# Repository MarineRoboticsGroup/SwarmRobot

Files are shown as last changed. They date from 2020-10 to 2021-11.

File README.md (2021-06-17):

# Swarm Robot

## Quick Start

This section will walk you through getting the software and networking set up for your robot to work. This assumes that your robot has been fabricated, assembled, and all components are properly connected. Much of the setup has been automated through the bash scripts provided in this repo. Start by cloning this repository into your home directory on the Intel Nuc and running the Nuc setup script.

### NUC Setup

<details>

This setup assumes that you have either Ubuntu 18.04 or 20.04 installed on the NUC. If not, I recommend following the official Ubuntu tutorials on [installing Ubuntu desktop from USB flash drive](https://ubuntu.com/tutorials/install-ubuntu-desktop#4-boot-from-usb-flash-drive) and [creating a bootable USB stick](https://ubuntu.com/tutorials/create-a-usb-stick-on-windows#1-overview).

Once this is done, the following instructions will walk you through the necessary steps to set up the NUC.

``` BASH
cd ~
git clone https://github.com/MarineRoboticsGroup/SwarmRobot.git swarm-robot
cd ~/swarm-robot/install
bash ./nucinstall.sh
```

**The bash script may sometimes fail while building the catkin workspace.** In this case: close the terminal, open a new terminal, and rerun `bash ./nucinstall.sh`

This will install all of the basic packages required, create a catkin workspace, clone all of the required repositories into this workspace, build the workspace, and remove the original repo cloned into the home directory. In addition, this performs some of the necessary network configurations of the Nuc to allow for use of this robot in a multi-robot network.

Then to allow for the robots to operate over a common network, change the namespace variables in the robot launch files such that each robot has a unique namespace. In general you can do this by changing the line `<arg name="namespace" default="mrg1" />` to `<arg name="namespace" default="<this robot's unique namespace name>" />`.

As of now the launch file(s) required to change are:

- ~/catkin_ws/src/swarm-robot/ros/launch/swarm_teleop.launch (Line 2)
- ~/catkin_ws/src/dynamixel-workbench/dynamixel_workbench_controllers/launch/dynamixel_controllers.launch (Line 4)
- ~/catkin_ws/src/orb_slam_2_ros/ros/launch/orb_slam2_d435_rgbd.launch (Lines 2, 8, 9)
- ~/catkin_ws/src/swarmbot_controller/launch/position_controller.launch (Line 2)

In addition, you will need to modify the ROS environment variables which specify the IP address of the ROS master and the NUC you are currently using. This was partially done in the install file, but the values will need to be modified to suit your desired setup and the specific IP of the NUC you are working on. This setup guide will cover the desired IP addresses you will want to set for several possible situations.

It will be valuable to know the `ifconfig` terminal command and understand which entries correspond to wireless and wired networks. Generally, if the network interface name starts with 'wl' (e.g. 'wlp0s20f3') then it is a wireless network. If the network interface name starts with 'en' (e.g. 'enp7s0f1') then it is an ethernet connection. Note that the format of the device name varies based on the operating system being used, so may not comply with the patterns shown above.

First open your `.bashrc` file in any editor and navigate to the bottom of the file.

``` BASH
nano ~/.bashrc
```

You will see two lines which look like this, where the values in <> are actually temporary values you will **need to change**:

``` BASH
echo "export ROS_IP=<Current NUC IP>" >> ~/.bashrc
echo "export ROS_MASTER_URI=http://<Master IP>:11311" >> ~/.bashrc
```

### IP Address options (NUC Setup)

<details>

#### Running a connected network with a separate computer

This is the most recommended and expected setup, where you will run the robots in a connected network. In this arrangement there will be an additional computer (either a laptop or a desktop which is connected to the same network shared by all of the NUCs) which will be the ROS master. In this scenario you will set the following:

\<Current NUC IP> = the IP address of the NUC on the shared wireless network.
\<Master IP> = the IP address of the connected laptop or desktop on the shared wireless network.

#### Running a connected network without a separate computer

This is like the previous scenario but without the additional computer, which one would likely use for monitoring. It is not immediately clear why someone would want to do this, but it will be listed anyways.

\<Current NUC IP> = the IP address of the NUC on the shared wireless network.
\<Master IP> = the IP address of any of the NUCs on the shared wireless network. **Note**: It is important that in this configuration that all robots must have the same \<Master IP> address.

#### Running a single robot

If you intend to only run this robot independently without having it connected to any other computers over a wireless network then you can set the `Current NUC IP` and `Master IP` to the same values. This could apply to a situation where you are running multiple robots but they are not connected with eachother and are running independently of one another. Such a scenario is possible in locations where it is difficult to establish a wireless network for one reason or another.

In this configuration we're assuming that the NUC is not connected to a wireless network at all.

\<Current NUC IP> = the IP address of the NUC on the shared ethernet network.
\<Master IP> = the IP address of the NUC on the shared ethernet network.

</details>

#### Configure the connection between NUC and Nano (NUC)

Next, you will want to configure the ethernet connection between the Intel NUC and the Jetson Nano. The easiest way to do this is by first making sure the Nano is powered on and connected to the NUC via ethernet. Then open your connections as such:

``` BASH
nm-connection-editor
```

Edit the wired connection between the NUC and the Nano (commonly named 'Wired Connection 1') and navigate to the IPv4 Settings Tab. Change method to `Shared to other computers` and click in the table of addresses to add a new entry. Set the entry to the following values - Address: 10.42.0.1 / Netmask: 24 / Gateway: (leave empty). This will set it such that the IP address of the NUC on the network made over this ethernet connection will always be `10.42.0.1`.

This can be done for all of the NUCs on the network, and will not cause any issues. This is because this is only their IP address for the local network connection they have with their connected Nano, so this IP address will not be reachable for any of the other NUCs in the larger ROS network. The connections between all of the NUCs on the ROS network will be shared over some local wireless network, on which it will have a separate IP address from the local ethernet network it shares with the Nano.

Finally, for convenience it is recommended to disable automatic updates, as described in [this line](https://www.omgubuntu.co.uk/2016/02/how-to-disable-automatic-update-ubuntu).

</details>

### Nano Setup

<details>

The nano setup should be mostly uninvolved. This setup assumes that the Jetson Nano has already been setup and is bootable. If not, follow [this tutorial](https://developer.nvidia.com/embedded/learn/get-started-jetson-nano-devkit#intro) to get started with the Nano.

We will first run a setup script that installs the necessary libraries for the Nano to work with the RealSense Camera.

``` BASH
cd ~
git clone https://github.com/MarineRoboticsGroup/SwarmRobot.git swarm-robot
cd ~/swarm-robot/install
bash ./nanoinstall.sh
```

*If having issues try running `bash ./nanoinstall.sh` again*. Sometimes it doesn't fully install the first time.

From here we just need to set up the wired connection between the Nano and the NUC. Make sure that there is an ethernet connecting the two devices and then open the connections configurations with the following command.

``` BASH
nm-connection-editor
```

There should be a single connection profile that says something like 'Wired Connection 1'. Edit this connection. Navigate to the `IPv4 Settings` tab. Change `Method` to *Manual*. In the Addresses table set the first (and only) row item to `Address = 10.42.0.25 | Netmask = 24 | Gateway = 10.42.0.1`.

This should be all that is necessary to set up on the Nano for our base configuration. You should check that the connection between the NUC and Nano is functioning by first trying to ping the NUC from the nano: `ping 10.42.0.1`. If this works then the Nano can find the NUC on the shared wired network between them. You can try ssh-ing into the NUC from the Nano and vice-versa to be more certain that the connections are setup properly, but as our networking is fairly simple ping-ing seems to generally be a sufficient test unless you notice further networking issues when trying to operate the robots.

</details>

### Quickstart Testing

This section will walk you through tests to check that the individual robot is
fully functional (at the component level).

#### Dynamixel and Joystick Testing (NUC)

<details>

This will require 2 separate terminals to run 2 different launch files. In
addition, make sure that a joystick (we use Logitech Wireless Gamepad F710) is plugged into the NUC.

##### terminal 1

``` BASH
roslaunch swarm_robot swarm_teleop.launch
```

##### terminal 2

``` BASH
roslaunch dynamixel_workbench_controllers dynamixel_controllers.launch
```

After running these two things and making sure the joystick controller USB is in
the NUC you should be able to control the robot's wheels by holding down the
left bumper (labeled LB) and moving the left joystick around. The other buttons
are currently mapped to different trajectories and should be avoided for now.

</details>

#### UWB Testing (NUC)

Make sure that the UWB is properly connected to the NUC. This means the
light-blueish USB is plugged in and the female jumper connectors on the other end
of this cable are attached to the UWB.

From here, if the `uwb_slam` repo has been cloned into `catkin_ws/src` and
properly built you should be able to test the connection to the UWB by running
`roslaunch uwb_slam_ros uwb_node.launch`. The output should look something like
the following:

``` BASH
.....................
.....................
hal:     UART: Rx 2 bytes: 0x3200
lmh:     UART: Received all 2 bytes, within 19.89 ms     OK
 [GetStatus]: Location data is ready = 1
 [GetStatus]: Node connected to UWB = 1
 [GetStatus]: UWB scan ready ready = 1
 [GetStatus]: User data received = 1
 [GetStatus]: User data ovr UWB sent = 0
 [GetStatus]: Firmware updating? = 0
hal:     UART: Tx 2 bytes: 0x0c00
lmh: rx started, timeout period changed to 18 ms
hal:     UART: Rx 2 bytes: 0x0c00
lmh:     UART: Received all 2 bytes, within 19.70 ms     OK
.....................
.....................
```

issues would be indicated by output that looks like the following:

``` BASH
.....................
.....................
lmh:     LMH_UARTRX_Init()...
hal:     UART: Init start.
hal: *** ERROR *** UART: Unable to open UART. 
hal: *** ERROR *** UART: Ensure it is not in use by another application
hal: *** ERROR *** UART: not initialized. 
lmh: *** ERROR *** UART: Received 0 bytes, expected 7 bytes, timed out in 1000 ms
lmh:     UART: Received length=0
 [GetStatus]: Unknown command or broken TLV.
 [GetStatus]: Location data is ready = 0
 [GetStatus]: Node connected to UWB = 176
 [GetStatus]: UWB scan ready ready = 252
 [GetStatus]: User data received = 127
 [GetStatus]: User data ovr UWB sent = 0
 [GetStatus]: Firmware updating? = 0
hal: *** ERROR *** UART: not initialized. 
lmh: UART: Received 0 bytes, until timed out in 1000 ms          OK
 [GetDistances]: Unknown command or broken TLV.
hal: *** ERROR *** UART: not initialized. 
^C[uwb_node-2] killing on exit
lmh: *** ERROR *** UART: Received 0 bytes, expected 7 bytes, timed out in 1000 ms
lmh:     UART: Received length=0
 [GetStatus]: Unknown command or broken TLV.
 [GetStatus]: Location data is ready = 0
 [GetStatus]: Node connected to UWB = 176
 [GetStatus]: UWB scan ready ready = 252
 [GetStatus]: User data received = 127
 [GetStatus]: User data ovr UWB sent = 0
 [GetStatus]: Firmware updating? = 0
hal: *** ERROR *** UART: not initialized. 
.....................
.....................
```

**Important, Read if Errors!**: the UWB as of now needs to be recognized as `/dev/ttyUSB0` to
function properly according to the uwb_slam repository that is used to interface
with it. This can be first checked by running a bash script inside this
repository `bash <swarm-robot-repo>/scripts/find_dev_port.bash`. The device in
question will be recognized as
'Silicon_Labs_CP2102_USB_to_UART_Bridge_Controller_0001'. However, this can cause
errors as the same USB to serial connector is used on the LiDAR we use. For this
reason, the LiDAR should be disconnected for now until the error has been fixed.
Both of these problems are current issues in this and the `uwb_slam` repos, and
should be fixed in the near future. Sometimes as a quick fix to the problem of
using the correct USB port we can use `sudo setserial -g /dev/ttyUSB0` but this
is not a perfect solution and only works when the LiDAR is not connected.

## Background

<details>

<summary> Please ignore this section until it has been cleaned up and corrected to accommodate the current codebase</summary>

Testing and implementing developed SLAM algorithms is difficult due to the accessibility of fully-formed robotic swarms, and the available swarms are often expensive or ineffective. The goal of our project is to design and build a robot that can communicate via ultra wideband and scale up to a larger swarm, with the capability of assessing SLAM algorithms and swarm experimentation.

IMG_20200811_091944 (1)

## Table of Contents

- [Design Principles](#design-principles)
- [Getting Started](#getting-started)
  - [Setting Up](#setting-up)
  - [Complete Instructions](#complete-instructions)
- [Hardware Setup](#hardware-setup)
  - [Connection Diagram](#connection-diagram)
  - [Multi-Robot Swarm Connections Diagram](#multi-robot-swarm-connections-diagram)
- [Network Setup](#network-setup)
  - [Setting Static IP Addresses for the NUC and Nano](#setting-static-ip-addresses-for-the-nuc-and-nano)
  - [Registering Dynamixel and RPLiDAR USB Ports](#registering-dynamixel-and-rplidar-usb-ports)
  - [Environment Variables and Host Key Setup](#environment-variables-and-host-key-setup)
- [Software Setup](#software-setup)
  - [ROS System Architecture Diagram](#ros-system-architecture-diagram)
  - [Configuring Master Launch File](#configuring-master-launch-file)
- [Resources](#resources)
  - [Dynamixel Instructions](#dynamixel-workbench)
  - [Intel RealSense Instructions](#ros-wrapper-for-intel-realsense-devices)
  - [RPLiDAR Instructions](#rplidar-ros-node-and-test-application)
- [Testing](#testing)
  - [Final Testing](#final-testing)
  - [Hello World for Individual Components](#hello-world-for-individual-components)
    - [RealSense](#realsense)
    - [Dynamixels](#dynamixels)
    - [RPLiDAR](#rplidar)
  - [Troubleshooting](#setting-up)
    - [Registering Dynamixels](#registering-dynamixels)
    - [Printing SolidWorks Drawings To Scale](#printing-solidworks-drawings-to-scale)
- [More Information](#more-information)
- [Authors](#authors)
- [Credits](#credits)
- [License](#license)

## Design principles

To accomplish our goal of designing and building a scalable robot with OTS technology for testing SLAM research through ROS-based software, there were several higher and lower-priority criteria.

1. Indoor SLAM testing
2. Inexpensive scalability
3. Robust design
4. UWB communications
5. Multiple sensing capabilities and room for more
6. Modular software programming
7. Multi-purpose design

Our design is centered around several principles, which are loosely ordered by importance above. Testing capabilities for SLAM were primarily important for research purposes, and scalability for testing swarms. A robust design is critical for repeated testing and multi-purpose experiments. Since our robot design's function is for indoors SLAM, the cheap yet effective ultra wideband was a solution for efficient indoor communications. Working in ROS, keeping the robot's software modular helps debugging while also keeping the system dynamic.




## Getting Started

### Setting up

- Intel NUC7i3DNHNC Mini PC
- MAXOAK Power Bank
- SinKeu Power Bank
- DWM1001 Development Board
- Intel RealSense Depth Camera D435i
- Jetson Nano Developer Kit
- DFR0315 RPLIDAR A1 Development Kit
- Dynamixel XL430-W250-T
- TurtleBot3 Burger Wheel Set
- Ball Caster
- U2D2
- Dynamixel Power Hub

All listed components are the main parts of the robot, but other parts are needed for power distribution and connection. These include: one or more power banks with the required ports, custom JST connectors, barrel jack cables, USB-micro cables, USB-C cables, USB-TTL adaptors, hook and loop velcro tape, wheels, ball caster (for stability), and plates (we custom designed and laser-cut the plates).



### Complete Instructions

Here are the step-by-step instructions for building a swarm robot. Starting from the finished physical build, you can follow the process to get your first official test and 'hello world' with all components and nodes running together. Each step is explained in further detail below, where the individual sections on hardware/build, networking, software, and troubleshooting are expanded on.

1. Build the robot using CAD design, labeled parts, and their corresponding cables. A full list of the components is available on the Drive, as well as in the hardware section below.
2. Download Ubuntu 18.04 onto a USB-key and boot up NUC with the key. You will need to connect the NUC to a monitor and keyboard, as well as a suitable power source.
3. Download the Jetson Nano Developer Kit SD Card Image to a micro-SD card (128 GB is more than enough) and follow Nvidia's set-up instructions to boot up the Nano. The Nano must also be connected to the necessary peripherals as above.
4. Connect back to the NUC, and connect the NUC to the local network (e.g. home network).
5. Download Chrome and install SSH through 'sudo apt-get install openssh-server'.
6. Clone the SwarmRobot github into your terminal space.
7. Run the NUC ROS install file from 'roboswarm' folder. For all files from the SwarmRobot github, make them executable with chmod +x the_file_name to run them.)
8. Run the NUC install and Nano install bash scripts on the NUC, as the control pc needs both the NUC and Nano's install software.
9. Connect the NUC and Nano via ethernet cable, and create an ethernet connection using nm-connection-editor (sudo nm-connection-editor to edit connection). Select ‘connect automatically’ and 'shared to other computers' on the NUC's end and ‘shared to other computers’.
10. Configure the address network under 'shared to other computers' with Address = 10.42.0.1, Netmask = 255.255.255.0, and Gateway = 10.42.0.1. Restart with 'sudo /etc/init.d/networking restart' back in terminal.
11. Connect to the Nano to the display and controls, set up ssh.
12. Clone into the SwarmRobot Github.
13. Run the Nano ROS install file and Nano install bash scripts from the cloned repository, and make sure to set the files as executable.
14. Source and create a catkin workspace for future use and availability (you can follow ROS Wiki's detailed instructions for creating a catkin workspace).
15. Set up the ethernet connection on the Nano's end by editing the connection in nm-connection-editor (sudo nm-connection-editor to edit connection). On the Nano's end, the ethernet is set to 'Automatic (DHCP)'. Restart the network with 'sudo /etc/init.d/networking restart'. If the connection isn't able to turn on, make sure that the NUC is powered on.
16. Set a static IP address for the Nano, explained in-depth in the Networking section. This is critical for connecting to and communicating with the Nano, as its IP address can shift to a range of IDs.
17. Configure the system's environment variables and host keys as explained in the Networking section.
18. If you're working on an Ubuntu machine (the remote control machine, not the NUC or Nano), X11 is automatically set-up (otherwise you can download an applicable X11 server). With ssh, you can work remotely from your pc after this point. X11 will become important with testing, as explained in the Final Tests section.
19. ssh -Y into the NUC (the command looks something like hostname@192.1...). We're using -Y to get the graphical display of the NUC, so we can visualize its GUI and visual outputs.
20. Add 'export ROS_IP=10.42.0.25' and 'export ROS_MASTER_URI=http://10.42.0.25:11311' to your sourcing, at 'gedit ~/.bashrc'. Here, you'll put in the IP address of your current Nano (which you can find via ifconfig).
21. Download Dynamixel Wizard 2.0 and register the Dynamixels by scanning for Protocol 2.0, Baud Rate 57600, and port USB0.
22. Once in, change the first Dynamixel's ID to 2, reverse direction, change Operating Mode to velocity-based (mode 1). Connect the second Dynamixel to the first (to daisy-chain their communication and power sources ) and keep its ID to 1 and change its Operating Mode as well.
23. Create new files as in 'Registering Dynamixel and RPLiDAR USB Ports' and copy in the respective information by following the instructions.
24. Go into the dynamixel_controller.launch and test_rplidar.launch files in your NUC's opt/ros/source... environment and hardcode the symlinks that you just created. This is done by simply writing in /dev/dynamixel and /dev/rplidar into the respective USB port fields, once again explained below in 'Registering Dynamixel and RPLiDAR USB Ports'.
25. Once in the dynamixel_controller launch file, you must also set use_cmd_vel to 'true' to be able to control the wheels.

This is the basic step-by-step guide to getting your Swarm Robot up and running! To begin testing and modifying the components, the next steps are explained in 'Testing'. Many of the above steps are reiterated and expanded on in later sections, but this beginning list is a good resource for general steps. The next few sections cover specific steps and troubleshooting tips, with a larger troubleshooting section at the end of this document.

If you have any questions, there are many great resources (including but not limited to): ROS Wiki, JetsonHacks, RealSense repo, Dynamxiel repo, Dynamixel Workbench e-manual, Nvidia forums, Stack Overflow, and general search queries. The MRG Drive also has additional resources and in-depth explanations. Feel free to reach out as well, either with Slack or through GMail, to the author.

## Hardware Setup

We based our design around similar principles as the Turtlebot3, a popular industry swarm robot. The major differences between the two are from additional sensing capabilities and different components, e.g. swapping the Jetson Nano for the Raspberry Pi computer.

IMG_20200811_091244 (1)


Main Parts:

- (ROS Control Module) Intel NUC7i3DNHNC Mini PC
- (Computer) Jetson Nano Developer Kit
- (UWB/Communications) DWM1001 Development Board
- (Camera) Intel RealSense Depth Camera D435i
- (LiDAR) DFR0315 RPLIDAR A1 Development Kit
- (Actuators) Dynamixel XL430-W250-T
- (Actuator Comms) U2D2*
- (Actuator Power) U2D2 Power Hub**
- (Battery #1) MaxOak 185Wh/50000mAh Power Bank
- (Battery #2) Sinkeu Power Bank
- (Robot Balance) Ball Caster
- (Robot Movement) Wheels + Tires

\* U2D2 is needed for Dynamixel-to-computer communication
\** U2D2 Power Hub supplies constant power to Dynamixels, necessary for required voltage and current

Cables:

- (NUC-UWB) USB-TTL Cable
- (NUC-Nano) Ethernet Cable
- (NUC-UWB) USB-micro Cable
- (NUC-DYN) USB-micro Cable
- (NUC-RPLiDAR) USB-micro Cable
- (DYN-DYN) JST Cable
- (DYN-U2D2) JST Cable
- (U2D2-PHB) JST Cable
- (NUC-MaxOak) Barrel Jack Connector
- (DYN-MaxOak) Barrel Jack Connector
- (Nano-SinKeu) USB-micro Cable
- (RealSense-Nano) USB-c Cable

### Connection Diagram




### Multi-Robot Swarm Connections Diagram



## Network setup

The step-by-step network set up is defined above, in the 'Getting Started' section. Here, you can find more detailed explanations and debugging tips.

### Setting Static IP Addresses for the NUC and Nano

Setting the Nano IP address permanently was tricky due to the wandering range of IP addresses that the DCHP would accept/look for. Most of the time, the Nano connected to the NUC using 10.42.0.25, but every so often, 10.42.0.26 might be the correct address.

The solution to this is to go into the nm-manager-editor settings on the Nano (through a hard connection to the monitor + keyboard/mouse) and 'MANUALLY' setting the IP configuration to 10.42.0.25 through netmask 255.255.255.255 (IPv4 settings).

Reload your new network settings via sudo /etc/init.d/networking restart.

### Registering Dynamixel and RPLiDAR USB Ports

As mentioned above, you must register the USB devices (for the Dynamixels and RPLiDAR) robustly so that they have a consistent USB id. This is because the USB devices are assigned dynamically as each device is plugged in e.g. /dev/ttyUSB0, /dev/ttyUSB1 etc…

To solve this, you can update /etc/udev/rules.d/* to match specific devices and create symbolic links:
/dev/rplidar
/dev/dynamixel

The two rules used:

99-dynamixel-workbench-cdc.rules

```bash
#http://linux-tips.org/t/prevent-modem-manager-to-capture-usb-serial-devices/284/2.

#cp rules /etc/udev/rules.d/
#sudo udevadm control --reload-rules
#sudo udevadm trigger

KERNEL=="ttyUSB*", DRIVERS=="ftdi_sio", MODE="0666", ATTR{device/latency_timer}="1", SYMLINK+="dynamixel"
```

88-rplidar.rules

```bash
# set the udev rule , make the device_port be fixed by rplidar
# ref: https://askubuntu.com/questions/1039814/how-to-create-a-udev-rule-for-two-devices-with-the-same-manufacturer-id-product
KERNEL=="ttyUSB*", ATTRS{idVendor}=="10c4", ATTRS{idProduct}=="ea60", MODE:="0777", SYMLINK+="rplidar"
```

Then to reload:

```bash
sudo udevadm control --reload-rules
sudo udevadm trigger
```

Then you can specify a port with each command:

```bash
cd ~/catkin_ws && catkin_make
roslaunch dynamixel_workbench_controllers dynamixel_controllers.launch use_cmd_vel:=true usb_port:=/dev/dynamixel
roslaunch rplidar_ros view_rplidar.launch  serial_port:=/dev/rplidar
```

### Environment Variables and Host Key Setup

To visualize the Nano and NUC's displays while controlling the robot, a few variables and exports need to be set up. The main variable file in /opt/ros/melodic/env.sh needs to be edited to include specific environment variables on ~/.bashrc.

export ROS_IP=10.42.0.25
export ROS_MASTER_URI=http://10.42.0.1:11311

Set up a group with additional machine info then include the file (which is included in the NUC launch file for conveniance).

```bash
  <group>
    <machine name="jetset_nano" address="10.42.0.25" user="sophia" password="sop
hia" env-loader="/opt/ros/melodic/env.sh" default="true" />
    <include file="/home/sophia/nanolaunch.launch" />
  </group>
```

All of the necessary code and configs must be set up on the master node that is invoking things remotely - the NUC in our case.

More helpful info here:
http://wiki.ros.org/roslaunch/XML/machine

SSH keys won't work by default, e.g. if you already connected to the Jetson through SSH. ROS needs a very specific kind of key in ~/.ssh/known_hosts.

If you get a weird error then you will need to remove this file (or at least the entry for the Jetson if you can find it) and then reconnect per these instructions:

```bash
ssh -oHostKeyAlgorithms='ssh-rsa' 10.42.0.25
```

## Software Setup

The ROS nodes and communications will be running on Ubuntu 18.04 with ROS Melodic. This can also be configured using previous versions of Ubuntu and ROS with most available software. Packages available for reference from ROS Wiki are listed below:

- Navigation Stack = http://wiki.ros.org/navigation
- Dynamixel Workbench Metapackage = http://wiki.ros.org/dynamixel_workbench
- RPLiDAR = http://wiki.ros.org/rplidar
- RealSense = http://wiki.ros.org/RealSense

### Configuring Master Launch File

Running multiple launch files with one or more arguments is a little more tricky. We found that you needed to pass in the specific launch file arguments through the component launch files. The minimum format for the master launch file is included in this repository, 'NUC.launch'. Since this is the master launch file, it also loops in the Nano's launch file, 'Nano.launch'. Instructions on setting up this exchange are explained in the 'Setting-Up' section, with a few troubleshooting tips below.

As an example, setting the USB port for the RPLiDAR isn’t passed in through NUC.launch file, rather you have to go into the test_rplidar.launch file and manually set it through nano test_rplidar.launch, from /dev/ttyUSB0 to /dev/rplidar.

#### ROS System Architecture Diagram



## Resources

### Dynamixel Workbench

This borrowed repository covers control and communication between Dynamixel motors, which can be done with one or daisy-chained together for shared power and movement. Deciding on software platforms largely depends on three things: type of Dynamixel motor, other components, and software configuration. Our system architecture was built using the Dynamixel Workbench due to larger control over the adjustments and fine-tuning. We suggest going through the Dynamixel Workbench for full instructions and support.

#### ROBOTIS e-Manual for Dynamixel Workbench

- [ROBOTIS e-Manual for Dynamixel Workbench](http://emanual.robotis.com/docs/en/software/dynamixel/dynamixel_workbench/)

#### Wiki for dynamixel_workbench Packages

- http://wiki.ros.org/dynamixel_workbench (metapackage)
- http://wiki.ros.org/dynamixel_workbench_controllers
- http://wiki.ros.org/dynamixel_workbench_operators
- http://wiki.ros.org/dynamixel_workbench_single_manager
- http://wiki.ros.org/dynamixel_workbench_single_manager_gui
- http://wiki.ros.org/dynamixel_workbench_toolbox

#### Open Source related to Dynamixel Workbench

- [dynamixel_workbench](https://github.com/ROBOTIS-GIT/dynamixel-workbench)
- [dynamixel_workbench_msgs](https://github.com/ROBOTIS-GIT/dynamixel-workbench-msgs)
- [dynamixel_sdk](https://github.com/ROBOTIS-GIT/DynamixelSDK)
- [open_manipulator](https://github.com/ROBOTIS-GIT/open_manipulator)
- [OpenCR-Hardware](https://github.com/ROBOTIS-GIT/OpenCR-Hardware)
- [OpenCR](https://github.com/ROBOTIS-GIT/OpenCR)

#### Documents and Videos related to Dynamixel Workbench

- [ROBOTIS e-Manual for Dynamixel Workbench](http://emanual.robotis.com/docs/en/software/dynamixel/dynamixel_workbench/)
- [ROBOTIS e-Manual for Dynamixel SDK](http://emanual.robotis.com/docs/en/software/dynamixel/dynamixel_sdk/overview/)
- [ROBOTIS e-Manual for OpenManipulator](http://emanual.robotis.com/docs/en/platform/openmanipulator/)
- [ROBOTIS e-Manual for OpenCR](http://emanual.robotis.com/docs/en/parts/controller/opencr10/)

Following the steps outlined in the Dynamixel Workbench e-manual worked successfully for us. Configuring the environment and packages for ROS was relatively simple, and it was possible to test the Dynamixels from the computer after a few tweaks outlined in debugging. These are important debugging steps that utilize Dynamixel Wizard 2.0 (available on Windows, Linux, and Mac) for long-term motor configuration before they can communicate with the NUC remotely.

Once properly set up (either with test computer or NUC), the Dynamixels can be controlled from the keyboard with a few Linux commands.

```bash
cd ~/catkin_ws && catkin_make
roslaunch dynamixel_workbench_operators wheel_operator.launch
roslaunch dynamixel_workbench_controllers dynamixel_controllers.launch use_cmd_vel:=true
```

<!-- ### ROS Wrapper for Intel RealSense Devices
TODO (alan) review this section and update

The Intel RealSense is a great camera for high-quality RGB and depth streams for 3D scanning and video capture. The integrated IMU sensor allows for improved navigation capabilities and motion tracking, useful for any SLAM testing. We went with the RealSense 435i for its global shuttering and larger field of view.
(Full workbench can be found at https://github.com/IntelRealSense/realsense-ros)

LibRealSense supported version: v2.29.0 (see [realsense2_camera release notes](https://github.com/IntelRealSense/realsense-ros/releases))

#### Installation Instructions

The simplest way to install on a clean machine is to follow the instructions on the [.travis.yml](https://github.com/intel-ros/realsense/blob/development/.travis.yml) file. It basically summarizes the elaborate instructions in the following 3 steps:

Step 1: Install the latest Intel&reg; RealSense&trade; SDK 2.0

- Install from [Debian Package](https://github.com/IntelRealSense/librealsense/blob/master/doc/distribution_linux.md#installing-the-packages) - In that case treat yourself as a developer. Make sure you follow the instructions to also install librealsense2-dev and librealsense-dkms packages.

OR

- Build from sources by downloading the latest [Intel&reg; RealSense&trade; SDK 2.0](https://github.com/IntelRealSense/librealsense/releases/tag/v2.29.0) and follow the instructions under [Linux Installation](https://github.com/IntelRealSense/librealsense/blob/master/doc/installation.md)

Step 2: Install the ROS distribution

- Install [ROS Melodic](http://wiki.ros.org/melodic/Installation/Ubuntu), on Ubuntu 18.04

Step 3: Install Intel&reg; RealSense&trade; ROS from Sources

- Create a [catkin](http://wiki.ros.org/catkin#Installing_catkin) workspace

```bash
mkdir -p ~/catkin_ws/src
cd ~/catkin_ws/src/
```

- Clone the latest Intel&reg; RealSense&trade; ROS from [here](https://github.com/intel-ros/realsense/releases) into 'catkin_ws/src/'

```bashrc
git clone https://github.com/IntelRealSense/realsense-ros.git
cd realsense-ros/
git checkout `git tag | sort -V | grep -P "^\d+\.\d+\.\d+" | tail -1`
cd ..
```

- Make sure all dependent packages are installed. You can check .travis.yml file for reference.
- Specifically, make sure that the ros package *ddynamic_reconfigure* is installed. If *ddynamic_reconfigure* cannot be installed using APT, you may clone it into your workspace 'catkin_ws/src/' from [here](https://github.com/pal-robotics/ddynamic_reconfigure/tree/kinetic-devel) (Version 0.2.0)

```bash
catkin_init_workspace
cd ..
catkin_make clean
catkin_make -DCATKIN_ENABLE_TESTING=False -DCMAKE_BUILD_TYPE=Release
catkin_make install
echo "source ~/catkin_ws/devel/setup.bash" >> ~/.bashrc
source ~/.bashrc
```

Note that setting this sourcing can complicate having more than one catkin workspaces, but for this project, it works well. -->

#### Usage Instructions

##### Start the camera node

To start the camera node in ROS:

```bash
roslaunch realsense2_camera rs_camera.launch
```

This will stream all camera sensors and publish on the appropriate ROS topics. Other stream resolutions and frame rates can optionally be provided as parameters to the 'rs_camera.launch' file.

If you're looking to test with more specific data-gathering modes, you can generate a pointcloud with the RealSense. Visualizing the camera output can be easily set up through Rviz, by launching Rviz in another terminal. There are a few steps to configuring the camera settings, shown below.

To start the pointcloud camera node in ROS:

```bash
roslaunch realsense2_camera rs-camera.launch filters:=pointcloud
```

1. Launch Rviz in separate terminal
2. Switch Fixed Frame to camera_link
3. Add in Image and PointCloud2
4. Designate Image Topic and Topic to the visual input that you want to generate the pointcloud from (it doesn't automatically select those options, which may result in 'no image found')

#### Published Topics

The published topics differ according to the device and parameters.
After running the above command with D435i attached, the following list of topics will be available (This is a partial list. For full one type `rostopic list`):

- /camera/color/camera_info
- /camera/color/image_raw
- /camera/depth/camera_info
- /camera/depth/image_rect_raw
- /camera/extrinsics/depth_to_color
- /camera/extrinsics/depth_to_infra1
- /camera/extrinsics/depth_to_infra2
- /camera/infra1/camera_info
- /camera/infra1/image_rect_raw
- /camera/infra2/camera_info
- /camera/infra2/image_rect_raw
- /camera/gyro/imu_info
- /camera/gyro/sample
- /camera/accel/imu_info
- /camera/accel/sample
- /diagnostics

### RPLiDAR ROS Node and Test Application

The RPLiDAR A1M8 from Roboshop is a great, inexpensive LiDAR with 360 degree FOV and a large ranging distance that integrates with SLAMAlg. It is also used on the TurtleBot3 Burger. Full workbench can be found at [rplidar-ros](https://github.com/robopeak/rplidar_ros)

Visit following websites for more details about RPLIDAR:

- [rplidar roswiki](http://wiki.ros.org/rplidar)
- [rplidar HomePage](http://www.slamtec.com/en/Lidar)
- [rplidar SDK](https://github.com/Slamtec/rplidar_sdk)
- [rplidar Tutorial](https://github.com/robopeak/rplidar_ros/wiki)

#### How to build RPLiDAR ros package

1) Clone this project to your catkin's workspace src folder
2) Running catkin_make to build rplidarNode and rplidarNodeClient

#### How to run RPLIDAR ROS package

There are two ways to run RPLIDAR ROS package
<!-- TODO talk about how the lidar can be configured -->

#### 1. Run RPLIDAR node and view in rviz

roslaunch rplidar_ros view_rplidar.launch (for RPLIDAR A1/A2)
or
roslaunch rplidar_ros view_rplidar_a3.launch (for RPLIDAR A3)

You should see the rplidar scan result in the rviz window.

#### 2. Run RPLIDAR node and view using test application

roslaunch rplidar_ros rplidar.launch (for RPLIDAR A1/A2)
or
roslaunch rplidar_ros rplidar_a3.launch (for RPLIDAR A3)

rosrun rplidar_ros rplidarNodeClient

You should see the rplidar scan result in the console

Notice: the different is serial_baudrate between A1/A2 and A3

#### RPLidar frame

RPLidar frame must be broadcasted according to picture shown in rplidar-frame.png

## Testing

### Final Testing

<!-- TODO (alan) rewrite this section to comply with latest version -->

<!-- Once everything is configured, you can run the NUC launch file to get all of the components moving! The Dynamixels are teleoperable with the w,a,s,d,x keys and all nodes are live (with the Jetson nodes ssh'd through the NUC ssh-key). If you're looking to go one step further and visualize the robot's camera and lidar data, this is where the X11 setup really comes in.

To do so, ssh -Y into the NUC and call roslaunch nuc.launch

- Once the program is running, generate a separate NUC terminal and run rviz.
- You can visualize the RealSense data (all the way from the Nano!) by inputting 'camera_link' and adding in 'Image'. Designate the Image 'topic' with your desired input and the realtime camera feed should appear in the bottom left screen.
- You can add in the laser scan data by then typing 'scan' where camera_link is (the camera feed will stay). Add in the option 'LaserScan' through the option 'published nodes'. Input its topic as /scan and a laser scan readout should appear.
- You can now drive the robot around with realtime camera imaging and laser output. -->

### Hello World for Individual Components

Outlined below is the 'Hello World' for controlling/testing individual components.

#### RealSense

1. Run roslaunch realsense2_camera rs_camera.launch to start the realsense node
2. Run realsense-viewer to open the graphical display (best method for testing because user can see camera output)
3. Run roslaunch realsense2_camera rs-camera.launch filters:=pointcloud and keep open
4. In another terminal, run rviz to generate 3D pointcloud
  a) Switch Fixed Frame to camera_link
  b) Add in Image and PointCloud2

Debugging: designate Image Topic and Topic to the visual input that you want to generate the pointcloud from (it doesn't automatically select those options, which may result in 'no image found')

#### Dynamixels

Once the Dynamixels are configured with Dynamixel Wizard 2.0 (explained in greater detail under 'Troubleshooting', you can control the motors through the terminal. Dynamixel Workbench allow for python and cpp, and we recommend following the manual procedures for a ROS-based platform from the Dynamixel-Workbench GitHub repository.

Summing up the process:

- There are three repositories to download (workbench, msgs, and SDK)
- Setup SDK and Workbench libraries with 64bit arch (skip sample code from SDK)
- Copy rules files, check USB port
- Finding Dynamixels is waste of time as it only registers one (don't be alarmed by that, only one is connected)
- Test connection with Workbench by

```bash
cd  ~/dynamixel-workbench/dynamixel_workbench_toolbox/examples/build
./position /dev/ttyUSB0 57600 1 (will rotate pi degrees 6 times)
```

#### RPLiDAR

The LiDAR starts spinning as soon as micro-USB is plugged into pc, and you can test the node control with roslaunch rplidar_ros view_rplidar.launch. This program generates a rviz graphical readout where pointcloud is continuously made from LiDAR data.

Debugging:

An error might occur where the RPLiDAR couldn't bind to the specified serial port /dev/tty/USB0. This seems to be common LiDAR problem, remedied through the command:

```bash
sudo chmod 666 /dev/ttyUSB0
```

This changes the permissions of RPLiDAR rules file from 0777 to 0666, as it automatically reverts to 0777 when the LiDAR starts running or is plugged in. Once the command is in, everything runs smoothly. (This is separate from long-term set-up with setting sym-links to the RPLiDAR USB port, aimed towards quick initial testing.)

### Troubleshooting

General:

- Be sure to use USB3.x for the RealSense camera, otherwise you will run into limitations on depth+rgb throughput when testing in ROS.
- Set Jetson to low power mode to run off of USB (board comes with jumper to switch to barrel-jack input, not needed for low-power mode.
- MaxOak auto-sleeps without enough current draw, keep RPLiDAR plugged in for initial testing and running.
- If NUC won't turn on try testing the power cables connecting it to the battery. Sometimes they are not fully in and result in a poor connection. Also, sometimes just try flipping the ends of the cable (switching what they are plugged into). It is unclear why this works, but it does :)

Dynamixels (in-depth explanation below):

- The Dynamixels require direct configuration from the Dynamixel Wizard 2.0 application, which can be downloaded onto any platform. For the computer to be able to communicate with each Dynamixel, we found that registering them on Wizard was the most simple.
  - After connecting the Dynamixels to the NUC and a power source, scan for the connected motors on the Wizard. The XL430-W250 motors that we used were registered with 57600 baud rate and Protocol 2.0.
  - Once they were registered via scanning, it was necessary to configure them to 'wheel mode' from the automatic 'joint mode'. This could be done through the control panel with 'Operating Mode', changing the mode to '1' or velocity-based. Editing the system controls is only possible when torque mode is turned off, but it should be turned on for running tests.
  - Since the motors are mirrored, it's necessary to configure them to run in the same direction. This can also be done through Dynamixel Wizard 2.0, by checking 'Reverse-drive mode'.
- Print Solidworks Drawings to scale using custom scale and pdf-poster generator
- Dynamixel threaded holes are only 4mm deep, can breach inner chamber if not careful

#### Registering Dynamixels

As mentioned above, you can register and configure the Dynamixel motors using Dynamixel Wizard 2.0. This was the most simple platform for a quick set-up, and runs on Windows, Linux, and Mac.

- Set up the Dynamixels with the U2D2, U2D2 Power Hub, and the power source.
- Select Dynamixel X and port COM4 (or the port that the Dynamixel automatically connects to via USB)
  - You can find the connected port on the pc using Device Manager
- It will appear to connect, then run a search using baud rate
- XL-430 connects with any baud rate, can go with the standard '57600'
- Once connected, test out connection with Control Table. Turn on Torque Enable and move around through Goal Position. You can also reverse direction of one or more motors to get opposite motors running in parallel.

Debugging: MaxOak will shut down if there's not a high enough current draw. When lights aren't on/power button hasn't been pressed in x amount of time, that's because the two main outputs shut down with 150 and 200 mA.

<!-- 
#### Printing SolidWorks Drawings To Scale

Printing a full-size drawing of a design can be helpful in the prototyping or manufacturing phase, depending on your set-up and available tools.

Here are some steps for successfully creating a to-scale representation:

1. Create the part in SolidWorks
2. Open as Drawing (DRWG)
3. Depending on the size of the part, make custom paper size (in multiples of 8.5"x11") if larger than letter paper
4. Put goal view on page and select 'scale to page'
5. Change page scale to be 1:1 (most printers aren't accurate enough to print 1:1. Print out a test measurement ex. a six inch line, and modify the first '1' to that value.)
6. Our printer's scale was closer to 1.03225:1, which I put into the custom scale properties
7. Save drawing as pdf
8. Open pdf in a pdf reader (make sure the app can print posters if part is larger than letter paper, I used Adobe Acrobat.)
9. Print as poster in pdf reader, spanning across pages with 100% scaling
10. Cut pages at lines and assemble paper design with tape for a simple to-scale drawing -->

## More information

Documentation is available on the MRG Drive with full instructions and explanations. If you have any questions that aren't answered from the GitHub or Google Drive, please feel free to reach out to Sophia Franklin on slack or at sophia.franklin@gmail.com.

<details>

## Authors

- **Sophia Franklin**
- **Alan Papalia**

## Credits

- **ROBOTIS-GIT/dynamixel-workbench**
- **kintzhao and the rest of the contributors for [rplidar-ros](https://github.com/robopeak/rplidar_ros)**
- **Intel and the contributors at [realsense-ros](https://github.com/IntelRealSense/realsense-ros)**
- **JetsonHacks at jetsonhacks.com**

## License

This project is licensed under the MIT License - see the
[LICENSE.md](LICENSE.md) file for details

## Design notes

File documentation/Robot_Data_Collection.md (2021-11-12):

# Steps for Collecting Data from a Single or Multi-Robot Set-up
---
### The SwarmRobots have been configured with a complete platform for both controlling and collecting data from the various on-board sensors and software. While there are many ways of running the robot’s programs, the optimal set-up is through the ROS binary for Procman. Procman-ROS is a platform for managing many programs on several computers at once, which can be used to control each function and sensor of the SwarmBots. 

### This write-up is designed with a master computer and one or more swarm robots in mind, however, it can be modified depending on the situation. From configuring the master-agent relationships between the robots, to replaying a ROSBag to visualize the collected data, these steps go through the full set-up process.
---
1. The master computer and agent robot networks must be configured properly in the bashrc file before any other software is downloaded.
    1. `sudo nano ~/.bashrc`
    2. ctrl+end
    3. Verify `export ROS_IP=<insert IP address here>` matches the computer’s IP address under wlp0 when running ifconfig
    4. Change `export ROS_MASTER_URI=http://<insert IP address here>:11311` to the IP address of the master computer
2. Download Procman-ROS on each of the robots and the master computer if not already installed.
    1. Procman-ROS depends on LCM, python2, and PyGTK
        1. LCM can be built from source through the github repository [link](https://lcm-proj.github.io/build_instructions.html)
        2. `sudo apt install python-minimal`
        3. `sudo apt install python-gtk2`
    2. `cd ~/catkin_ws/src`
    3. `git clone https://github.com/MarineRoboticsGroup/procman_ros.git`
    4. `cd procman_ros`
    5. `mkdir build && cd build`
    6. `cmake ..`
    7. `make -j4`
    8. `catkin build`
    9. `source devel/setup.bash`
3. Assuming that the required software for each device is installed and built, and each robot’s devices are connected, Procman-ROS can be fired up.
    1. If the UWB runs into conflicts with the RPLiDAR, see "Guide to Configuring Indistinct USB/UART Conflicts"
    2. Verify that the Joy ROS package is installed and running on the robot to be teleoperated. If not, `sudo apt-get install ros-melodic-joy`
    3. On each robot, attach a monitor + keyboard + mouse (preferably Bluetooth for ease of access)
        1. Alternatively, ssh into each robot once it's powered on through the master computer (eg. the main laptop). ssh <robot name>@<ip address> for headless set-up
    4. For each robot agent, type in `rosrun procman_ros deputy`
    5. Launch `roscore`
    6. `cd ~/catkin_ws/src/procman_ros/test` (where the Procman-ROS launch file script should be written)
    7. For the master computer, type in `rosrun procman_ros sheriff swarm_manager_3robot.cfg` as well as `rosrun procman_ros deputy`
        1. If the master computer is running anaconda, run `conda deactivate` to avoid python conflicts
4. With Procman-ROS configured on each respective robot and the master robot, data collection can begin with several commands.
    1. Each robot should be visible in the Procman-ROS GUI up on the master robot
    2. Start all processes/devices required for data collection on all running robots
    3. In a separate terminal, record a rosbag
        1. The standard Swarm Robot rosbag is recorded via `rosbag record tf rtabmap/odom susan/uwb_msg tf_static camera/color/image_raw/compressed rtabmap/mapPath rtabmap/mapGraph susan/laser` eg. using Susan
    4. The information recorded in the rosbag can either be all published topics with `-a` or the specific topics listed after `rosbag record`
        1. The rosbag will save to whichever location the command is run in
        2. If RTABMap isn’t running through the Procman-ROS GUI, ssh into the robot’s terminal and start RTABMap from there. This output will still be recorded through rosbag record
            1. RTABMap output can be verified by `rostopic echo /rtabmap/odom` in the main terminal
            2. UWB output can be verified with `rostopic echo /<robot name>/uwb_msg`
5. Once a satisfactory dataset has been recorded, its output can be analyzed with Rviz.
    1. Play back the recorded rosbag, to simulate real-time data collection, with rosbag play <name of recorded rosbag>
    2. Simultaneously, launch `rviz`
        1. rviz will only display the rosbag's data if all running processes through Procman-ROS are stopped completely
    3. Add in all topics to be visualized through the broadcasted topics option
    4. Repeat steps as needed to go through different subsets of data from the robot’s collected information

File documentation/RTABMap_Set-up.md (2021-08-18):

# Setting Up Complete RTABMap System on the SwarmRobots
---
### Our current system operates with a minimal RTABMap set-up, as we found the binary to be most robust for our data collection and analysis needs. While RTABMap can be built from source, we encountered several dependency conflicts that didn’t successfully lead to data collection and visualization output. 

### Through the rtabmap-ros binary, we established a working odometry collection pipeline and data collection/visualization set-up that can be reproduced reliably through the steps below. These steps include methods from several sources and write-ups, which are linked below for additional information.
---
1. Delete previous software for the Intel RealSense d435i, including the ROS binary for the realsense and its corresponding SDK.
    1. `sudo apt-get remove ros-melodic-realsense2-camera`
    2. Go through the operating ROS workspace and `rm -rf` any realsense-related directories eg. realsense-ros, librealsense, librealsense2, to minimize version conflicts and repeats (these will be rebuilt at a later point)
2. For a clean, dependable build, it was found necessary to purge the current ROS set-up to ensure fully-maintained dependencies and software versions. This was done by purging all related ROS software and rebuilding completely.
    1. `sudo apt-get purge ros-*`
    2. `sudo apt-get purge python-ros*`
    3. `sudo apt-get autoremove`
3. Now that all previous ROS software has been removed, it can be reinstalled as usual
    1. `sudo sh -c 'echo "deb http://packages.ros.org/ros/ubuntu $(lsb_release -sc) main" > /etc/apt/sources.list.d/ros-latest.list'`
    2. `curl -s https://raw.githubusercontent.com/ros/rosdistro/master/ros.asc | sudo apt-key add -`
    3. `sudo apt update`
        1. If the robot is unable to update, upgrade, or later on, install select applications, see "Common Bugs and Solutions for the Swarm Robots" under "Unable to Download Certain Packages (Ubuntu)".
    5. `sudo apt upgrade`
    6. `sudo apt install ros-melodic-desktop-full`
    7. `echo "source /opt/ros/melodic/setup.bash" >> ~/.bashrc`
    8. `source ~/.bashrc`
    9. `sudo apt install python-rosdep python-rosinstall python-rosinstall-generator python-wstool build-essential`
    10. `sudo apt install python-rosdep`
    11. `sudo rosdep init`
    12. `rosdep update`
4. Following the minimal install and set-up required to run SLAM via RTABMap on an Intel realsense D435i, there are several binaries to install before getting the system running
    1. `sudo apt-get install ros-melodic-realsense2-camera`
    2. `sudo apt-get install ros-melodic-imu-filter-madgwick`
    3. `sudo apt-get install ros-melodic-rtabmap-ros`
    4. `sudo apt-get install ros-melodic-robot-localization`
    5. `sudo apt-get install ros-melodic-octomap-rviz-plugins`
5. Realsense-ros also requires the librealsense SDK for camera operation and streaming settings
    1. `cd ~/catkin_ws/src`
    2. `sudo apt-get install git libssl-dev libusb-1.0-0-dev pkg-config libgtk-3-dev`
    3. `git clone https://github.com/IntelRealSense/librealsense.git`
    4. `mkdir build && cd build`
    5. `cmake ../`
    6. `sudo make uninstall && make clean && make && sudo make install`
    7. `cd ../..`
    8. `catkin build`
6. Finally, the main RealSense launch file must be configured for odometry data, as it combines accelerometer and gyroscope readings to output odometry
    1. `cd /opt/ros/melodic/share/realsense2_camera/launch`
    2. `code .` (call for VSCode)
    3. Within rs_camera.launch, change enable_gyro, enable_accel, enable_infra, enable_infra1, and enable_infra2 to “true”
    4. `cd`
    5. `source ~/.bashrc`
7. RTABMap is now fully set-up with the minimal binaries required for odometry output and RGB-depth mapping
    1. The collection and analysis to follow have been documented in Odom Data Collection/Conversion/Analysis Documentation
    2. It’s worth noting that these steps should lead to a working data collection and analysis setup from the host pc (ie. the robot’s onboard computer). However, several issues were encountered when implementing a multi-robot program manager such as Procman-ROS.	
    1. These issues were resolved by ssh-ing into the robot’s computer to run RTABMap remotely, which could still be picked up when recording a ROSBAG on the master computer.

### Additional Documentation

- Debugging: https://answers.ros.org/question/361445/rtabmap-tutorial-odometry-died-on-startup-noetic-xtion-u2004-beginner/ 

- RTABMap set-up: https://github.com/IntelRealSense/realsense-ros/wiki/SLAM-with-D435i

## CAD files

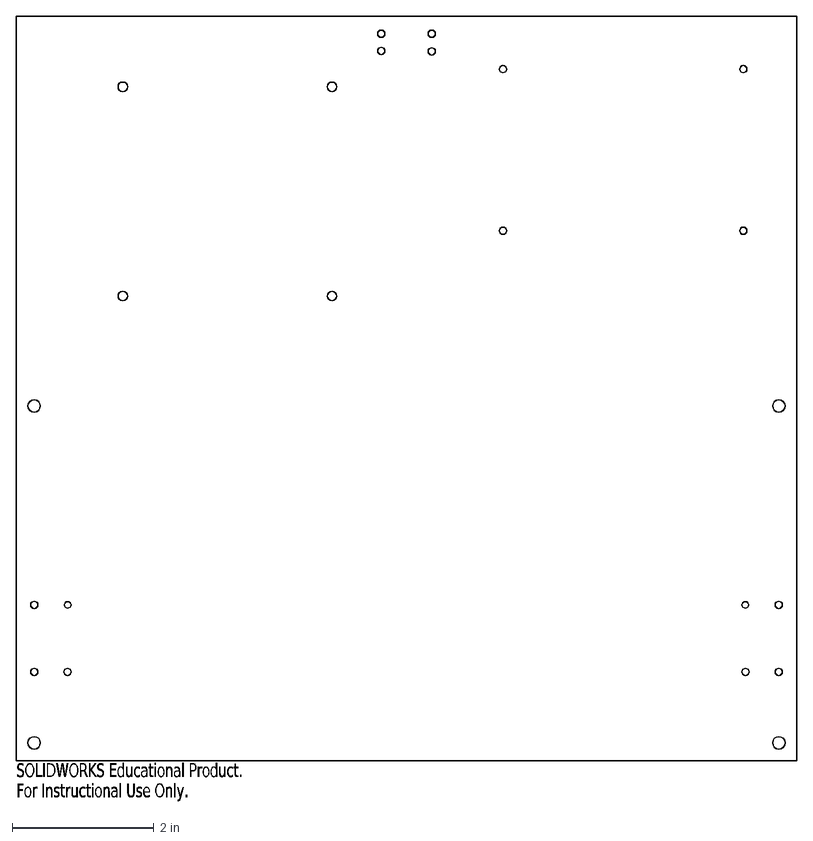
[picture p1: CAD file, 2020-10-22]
manufacturing/Final_bottom_plate_drawing.DXF
SOLIDWORKS Educational Product.
For Instructional Use Only.

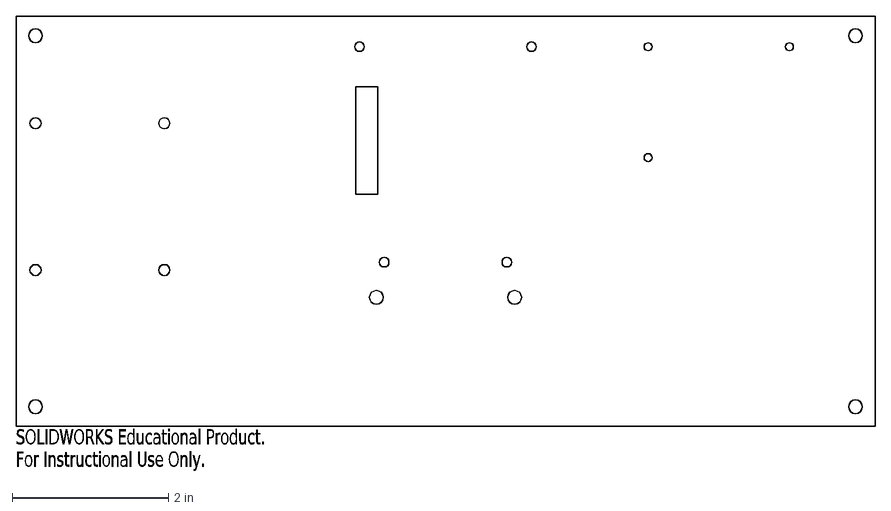
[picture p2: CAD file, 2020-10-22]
manufacturing/Final_top_plate_drawing (1).DXF
SOLIDWORKS Educational Product.
For Instructional Use Only.

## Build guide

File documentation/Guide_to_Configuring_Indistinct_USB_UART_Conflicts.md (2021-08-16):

# Guide to Configuring Indistinct USB/UART Conflicts
---
### For many large-scale manufactured devices, the low-cost computing chips inside are often bought and integrated from another manufacturer. This can result in labeling and ID conflicts, especially when dictating a computer’s USB communications with multiple devices that have the same chip. For assigning device IDs, the computer cannot distinguish between identical chips (where all distinguishable information is attained), and the devices will either not function at all or only sporadically.

### Our solution to this common issue is long-lasting and robust, where we utilize the chip’s software platform to modify a particular setting to differentiate between two devices, an RPLIDAR A1M8 with a Decawave DM1001 board. This unique setting can be implemented as the modified device’s ID, which can be configured to route the USB assignment, resulting in a functioning and unique computer system.
---
1. Download Simplicity Studios (version 5) from Silicon Labs onto a machine running Windows
    1. Windows is required, as Ubuntu build isn’t fully set-up, and several crucial functions for modifying USB/UART device IDs aren’t available as a result
    2. Both version 4 and 5 are available, however, only version 5 offers the necessary ID information access 
2. After setting up an account on Simplicity Studios, connect the device through USB that’s going to be modified
    1. It should show up in “Connected Devices” with its identifying information (including serial number, which we will be changing)
    2. Press Start -> Create New Project -> Xpress Configuration Project
3. The new project, which consists of the device’s current information, has unset fields for IDs including: vendor ID, product ID, manufacturer string, product string, and serial string
    1. Changing the VID (vendor ID) or PID (product ID) is discouraged, so it’s best to change the serial string for dependable identification
        1. The serial string is listed as “an optional string that is used by the host to distinguish between devices with the same VID and PID combination”
4. Change the serial string to a random yet memorable number that wouldn’t be used by any Silicon Lab devices (eg. 0001, 0002 wouldn’t be safe IDs but 1111,2222,3333,4567 etc. would be)
5. Enter the string, press save, and program the new ID to the device
    1. This process should take under a minute
    2. It’s worth noting that some devices can only be programmed to once. Check if the device/chip are a one-time programmable set-up or multi-time programmable, as this affects the number of attempted modifications available
6. Now, the device’s serial ID is modified to a unique value that won’t conflict with the other, non-unique Silicon Labs devices
    1. Repeat this process n-1 times for n devices with the exact same chip
7. Transfer these edits to the corresponding device’s rules files with a new attribute: ATTRS{serial}==”updated serial number of device”
    1. The new rules files are:
        1. KERNEL==”ttyUSB*”, ATTRS{idVendor}==”10c4”, ATTRS{idProduct}==”ea60”, ATTRS{serial}==”updated serial number of rplidar”, MODE:=0777, SYMLINK+=”rplidar
        2. KERNEL==”ttyUSB*”, ATTRS{idVendor}==”10c4”, ATTRS{idProduct}==”ea60”, ATTRS{serial}==”0001”, MODE:=”0777”, SYMLINK+=”uwb”
        3. Repeat these edits with the required format for each device
8. Save and transfer these edits with the command “sudo udevadm control --reload-rules && udevadm trigger”
9. Unplug all of the devices, then plug them back in again
    1. To verify the process, the UWB and RPLiDAR symlinks /dev/usb and /dev/rplidar should both be visible with ` ls /dev/uwb /dev/rplidar` 
    2. UWBs can occasionally be defective - if the UWB symlink is missing, make sure the USB port can see the device with ` udevadm info --attribute-walk --path=/sys/bus/usb-serial/devices/ttyUSBn`  where n is bus 0,1, or 2
10. Replace all of the ` /dev/ttyUSB0`  paths with ` /dev/rplidar`  for corresponding rplidar files (these were default paths initialized with the devices)
    1. All of the files to be edited are in ` ~/catkin_ws/src/rplidar_ros/launch` 
    2. Access all files for easy editing with ` code .` , which opens vscode editor
11. Save these edits and recompile the system by running ` cmake .. ; make -j`  in ` ~/catkin_ws/src/rplidar_ros/launch` 
12. The UWB/RPLiDAR configurations can be verified by running roslaunch rplidar_ros rplidar.launch and roslaunch uwb_slam_ros uwb_node.launch

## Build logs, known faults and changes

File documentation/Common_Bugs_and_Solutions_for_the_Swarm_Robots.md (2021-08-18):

# Common Bugs and Solutions for the Swarm Robots

## UWB or LiDAR USB Conflicts:
---
### Error Message: 
ERROR *** UART: Unable to open UART
Ensure it is not in use by another application
Not initialized. 
Received 0 bytes, expected 7 bytes, timed out in 1000 ms

### Solution:
The symlinks created for the UWB and LiDAR aren’t initialized, so the initial problem of dynamic USB-ID naming has incorrectly assigned the two devices.
Refer to the **Guide to Configuring Indistinct USB/UART Conflicts** documentation.

## RealSense Setting Configurations:
---
### Error Message:
No odom data found
No RGB data found

### Solution:
The main RealSense launch file, rs_camera.launch, hasn’t been configured with correct gyro/accel and infra1/infra2 settings.
Refer to the **Setting Up Complete RTABMap System on the SwarmRobots** documentation.

## Robot Roslaunch Frozen Commands:
---
### Error Message:
Terminal freezing upon roslaunch command
Output only when quitting via “Ctrl-C”

### Solution:
The ROS_IP and ROS_MASTER_URI likely haven’t been set to the IP address of the current wifi network.
Using ifconfig and sudo nano ~/.bashrc, configure the respective IP settings and source the changes using source ` ~/.bashrc` or simply closing and reopening the terminal.

## Running Roslaunch and Python Library Not Found:
---
### Error Message:
Python library name not found

### Solution:
Anaconda and its respective python versions and shells conflict with certain programs and roslaunch commands.
Quit the terminal Anaconda session with conda deactivate.

## No Odometry Data Available:
---
### Error Message:
E: Did not receive data since 5 seconds! 

### Solution:
When analyzing a rosbag of recorded RTABMap data, there may appear to be zero odometry readings collected.
RTABMap occasionally loses odometry in the data collection process, as its RGB-depth pointcloud projection can be broken if the camera is moved too quickly or sharply.
This situation can be confirmed by playing the rosbag back and showing the collected odometry measurements through ` rostopic echo /rtabmap/odom`.
If the messages are all zero values, then redo the rosbag recording with more attention to the recording methods.

## Unable to Download Certain Packages (Ubuntu):
---
### Error Message:
E: ubuntu apt-get unable to fetch some archives 404
E: Unable to fetch some archives, maybe run apt-get update or try with --fix-missing?

### Solution:
Some packages from certain repositories are blocked from installing on the computers, depending on the initial settings of the ubuntu instance.
This can often be solved by disabling Secure Boot within BIOS Boot Configuration settings.
If the above step doesn’t solve it, make sure the sources.list file in /etc/apt directory is updated to a current file version. An example sourcse.list file is uploaded under 'Documentation' from one of the robots. Simply replace the sources.list file within its directory, and after sourcing the set-up and re-opening terminal, the computer should successfully install all software and updates.

## Zero-Value Odometry to Plaza Format Data:
---
### Error Message:
ValueError: Found zero norm quaternions in `quat`.

### Solution:
This error comes up in the post-processing stage, where when converting from rtabmap/odometry format to plaza format, the quaternion transform is unable to work with zero-valued data.
There’s a method written into the format conversion program that should skip these values, which still maintains the majority of the data due to minimal zero values (eg. 1-2 zeros in a medium dataset).

## Unable to Install pyGTK:
---
### Error Message:
E: Unable to locate package pygtk
pyGTK stuck on dependencies that are unable to be resolved
	
### Solution:
` sudo apt install python-gtk2 python-gtk2-dev`
Reference (https://itsfoss.community/t/solved-pygtk-installation/2781)

## Unable to Install LCM:
---
### Error Message:
Unable to build LCM from source

### Solution:
` git clone https://github.com/lcm-proj/lcm.git
cd lcm
mkdir build && cd build
cmake ..
make -j2
sudo make install
Make sure all required dependencies are installed and built (build-essential, libglib2.0-dev, cmake)
echo $LCM_LIBRARY_DIR > /etc/ld.so.conf.d/lcm.conf`
Reference (https://lcm-proj.github.io/build_instructions.html)

## Realsense Data Overflow:
---
### Error Message:
Hardware Notification: 1.55068e+12, Error, Unknown Error

### Solution:
This error usually occurs when the USB-C to USB-A cable is rated 2.0 as opposed to the required 3.0. 
By switching out the cable for a 3.0 lightning cable, the overflow is contained.
Verify that the USB port is also powered, and that the RealSense is detected with rs-enumerate-devices.
If the camera is not found, unplug and replug the camera. realsense-viewer is also built into the SDK for debugging and verification purposes.

## Python Version Conflicts:
---
### Error Message:
ImportError: dynamic module does not define init function (PyInit__tf2)

### Solution:
If there are multiple versions of python running in the same environment, conflicts between version-based packages arise when running certain programs.
Python3 shouldn’t be running through ROS as ROS2 goes along with Python3.
Anaconda is also built with Python3, so it’s important to be aware of the current version as well as build of involved software.

## RealSense Software Missing:
---
### Error Message: 
(synthetic-stream.cpp:48) Exception was thrown during user processing callback: Out of frame resources!

### Solution:
This error can come up if RealSense software hasn’t been properly installed. Whether the binary or SDK haven’t been installed or built correctly, or certain packages and dependencies are broken, this situation is often fixed by complete reinstall of all RealSense software.
Refer to the **RTABMap Set-up** documentation on setting up all required RealSense software successfully.

## RTABMap Process Dies After Start-Up:
---
### Error Message:
Process has died [pid 6785, exit code -6, cmd /opt/ros/noetic/lib/rtabmap_ros/rgbd_odometry rgb/image:=/camera/rgb/image_rect_color depth/image:=/camera/depth_registered/image_raw rgb/camera_info:=/camera/rgb/camera_info rgbd_image:=rgbd_image_relay odom:=/odom imu:=/imu/data __name:=rgbd_odometry __log:=/home/aug/.ros/log/d90a0fe6-f490-11ea-a0cb-6b5fc5d13082/rtabmap-rgbd_odometry-1.log]. log file: /home/aug/.ros/log/d90a0fe6-f490-11ea-a0cb-6b5fc5d13082/rtabmap-rgbd_odometry-1*.log

### Solution:
While this error can come up for several different reasons, one of the Swarm Robots encountered exit code -6 because of a set-up error resulting from multiple versions of OpenCV.
Both OpenCV 4.5 and OpenCV 3.2 were running in the same Ubuntu environment, causing RTABMap to die after the launch file was called through roslaunch.
Running the command ` find / 2>/dev/null | grep libopencv | egrep "4.5|3.2" | grep ".so" | more`  can clarify if two versions of OpenCV are floating around. 
If this is the case, remove the unnecessary system (which can be determined depending on the build versions of reliant software).

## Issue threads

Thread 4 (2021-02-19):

USB device collision for USB to Serial Adapters

alanpapalia, 2021-02-19:
The USB to serial adapters used for the Lidar and the UWB cables are identical and as such any rules in `/etc/udev/rules.d/` cannot specify the difference between the two of them. The suggested improvement is including a step in the startup procedure where the programmer from Silicon Labs is used to change the serial number of one of the devices so that they differ and the serial number can be used to specify the difference between devices. The procedure for how to do this is outlined in the comments in the link below:

https://askubuntu.com/questions/1039814/how-to-create-a-udev-rule-for-two-devices-with-the-same-manufacturer-id-product
**Note**: this approach seems to require a windows environment

Other potentially relevant links:
https://unix.stackexchange.com/questions/144029/command-to-determine-ports-of-a-device-like-dev-ttyusb0
https://askubuntu.com/questions/49910/how-to-distinguish-between-identical-usb-to-serial-adapters
https://forum.odroid.com/viewtopic.php?t=25006
https://www.silabs.com/community/interface/forum.topic.html/cp210x_not_workingo-5qdu
https://electronics.stackexchange.com/questions/338883/identical-cp210x-usb-serial-converter-conflict

sophiafranklin, 2021-08-10:
See "Guide to Configuring Indistinct USB_UART Conflicts.docx" in SwarmRobot/documentation for developed solution.

alanpapalia, 2021-08-10:
When that's converted to Markdown we'll take a quick look over the docs and close the issue :)

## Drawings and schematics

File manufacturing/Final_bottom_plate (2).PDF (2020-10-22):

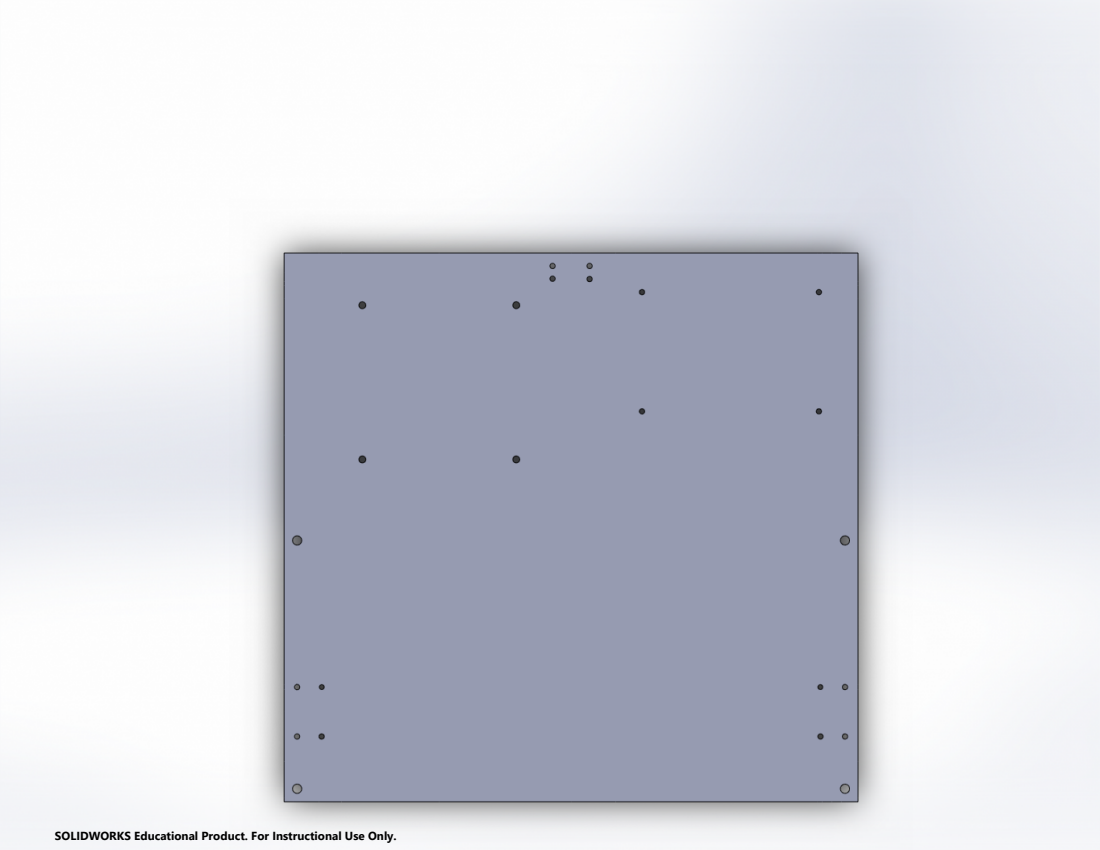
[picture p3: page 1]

SOLIDWORKS Educational Product. For Instructional Use Only.

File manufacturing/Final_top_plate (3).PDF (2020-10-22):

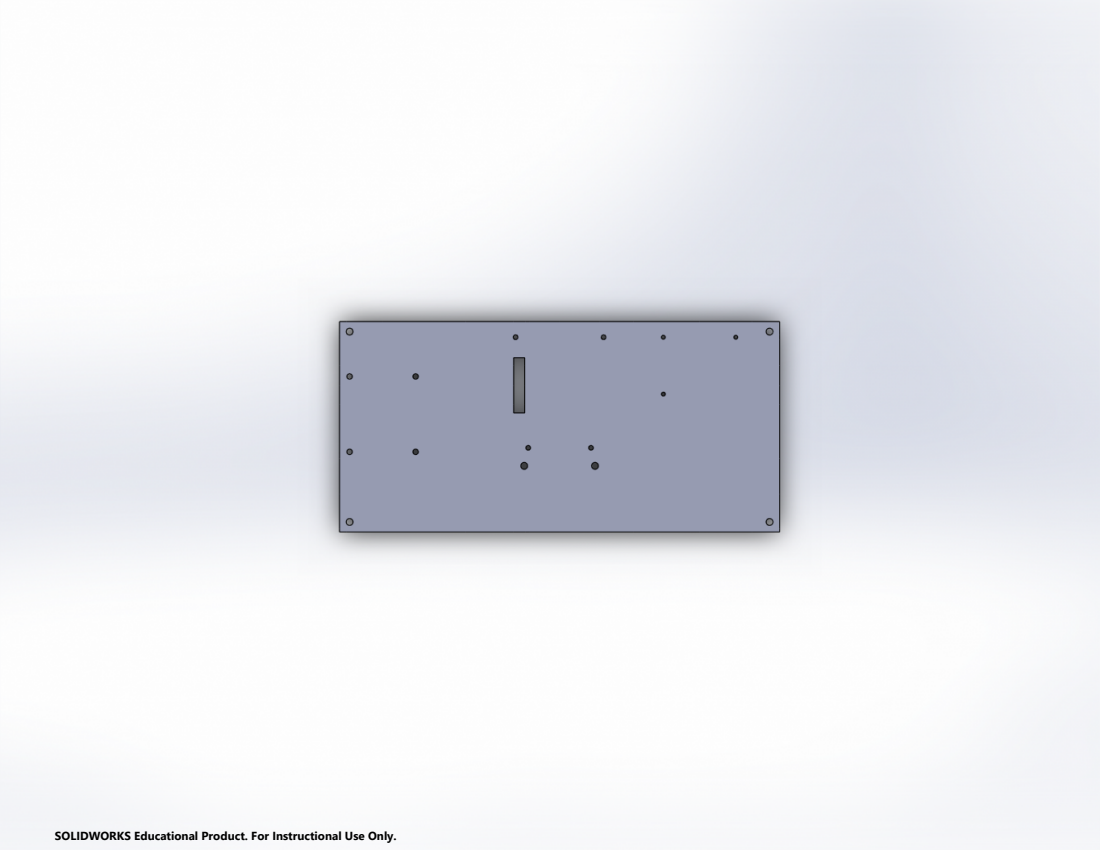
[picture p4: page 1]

SOLIDWORKS Educational Product. For Instructional Use Only.

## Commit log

2020-10-23 modified dynamixel workbench setup to use custom file to allow for multiple USB devices (U2D2 and RPlidar)
2020-10-24 restructured and started to add new node to allow for predesigned motions
    [Final_bottom_plate_drawing.DXF, Final_top_plate_drawing (1).DXF]
2020-10-28 added scripts to convert rosbags into plaza dataset format
    [pyvenv.cfg]
2020-10-29 removed unnecessary files and updated gitignore
    [pyvenv.cfg]
2020-12-10 updated convert bag to plaza file to write range measurements in meters instead of millimeters
2021-02-19 reformatted scripts and added utility script to check usb devices
2021-08-10 Convert odometry from RTABMap to Plaza format
